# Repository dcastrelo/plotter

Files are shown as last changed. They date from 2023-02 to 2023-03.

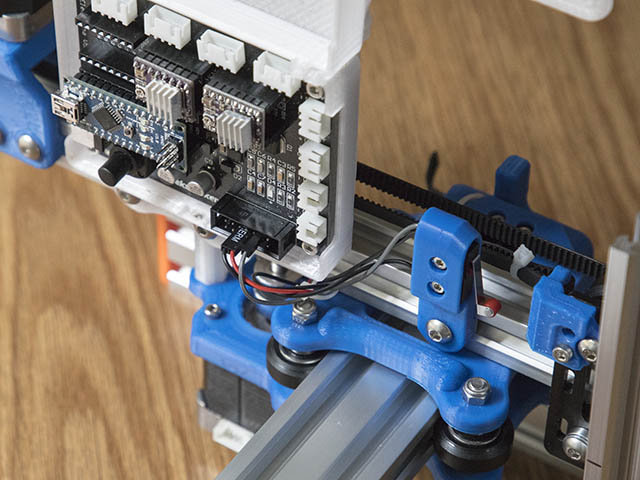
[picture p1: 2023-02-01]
images/IMG_1413_640x480.jpg

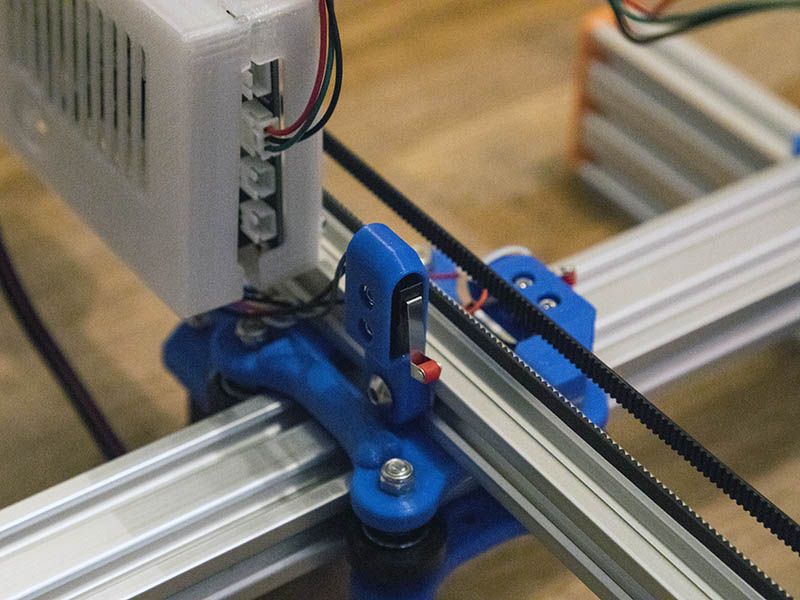
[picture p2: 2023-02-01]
images/IMG_1424_800x600.jpg

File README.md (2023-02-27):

# plotter para usar con laser o lo que sea

proyecto: https://openbuilds.com/builds/horizontal-cantilever-or-vertical-diode-laser-engraver.10031/
fork de https://www.thingiverse.com/thing:4934772

listado de partes: https://docs.google.com/spreadsheets/d/1wXE9ehnmEfAuOU7LIpCEzy9SvMc0fRSBS328PcNFEXU/edit?usp=sharing

Guia de armado
https://github.com/dcastrelo/plotter/blob/main/Assembly_Guide_for_Cantilever_Laser_Engraver_V821.2.pdf

vamos a hacer el modelo D_2040_2040

URL con info para lidiar con el firmware y poder usar el servo como Z

https://www.instructables.com/How-to-Control-a-Servo-Using-GRBL/

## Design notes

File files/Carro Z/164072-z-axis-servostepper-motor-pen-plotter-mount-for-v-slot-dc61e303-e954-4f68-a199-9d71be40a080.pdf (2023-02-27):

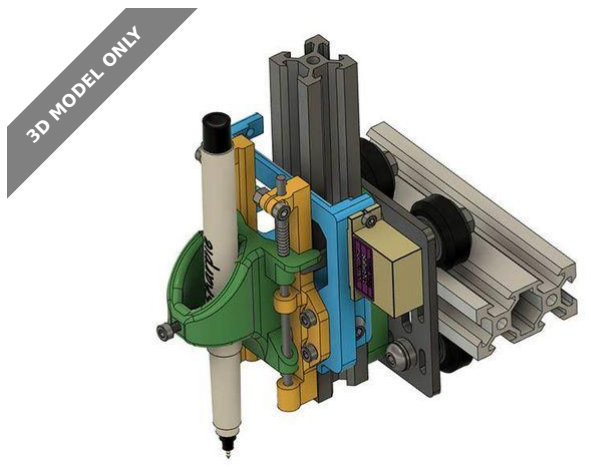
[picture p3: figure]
3D MODEL ONLY

# Summary

12/28/2020 Update: I added the file *RP_200411_Servo_Z_Dual_X.cfg**

that has my klipper configuration using the servo...

Art & Design (https://www.printables.com/model?categoryId=13) | > | Other Art & Designs (https://www.printables.com/model?categoryId=41)
Tags: fusion360 | arduino | penholder | penplotter | cncplotter

### 12/28/2020 Update:

I added the fileRP_200411_Servo_Z_Dual_X.cfg* that has my klipper

configuration using the servo for the Z-axis for reference.

Z-axis servo/Stepper motor Pen Plotter mount for V-Slot

I needed a pen mount for the Rolling Plotter I am designing and https://

www.thingiverse.com/thing:2349232 was pretty much what I wanted

except I needed it to mount to a 2020 V-slot. I redrew it in fusion 360 like it

was & then modified it to work for my design. I had some troubles getting

the servo to work with Marlin firmware, so I made a couple of other

mounts to use a nema17 pancake stepper & a 28BYJ-48 stepper motor. I

then found a way to use the servo with klipper firmware, but might use a

stepper motor later. I found the models of the servo, sharpie, & 28BYJ-48 geodave (https://www.printables.com/social/231754/about)

# Z-axis servo/ Stepper motor Pen Plotter mount for V-Slot

VIEW IN BROWSER (https://www.printables.com/model/164072-z-axis-servostepper-motor-pen-plotter-mount-for-v-)

updated 12. 4. 2022 | published 7. 4. 2022

stepper motor on grabcad, but didn't include them in the fusion 360

assembly file here.

The build log of my printer can be found here: https://openbuilds.com/

builds/a-rolling-plotter.9207/ (https://openbuilds.com/builds/a-rolling-plotter.9207/)

Here is a video of my plotter in action.

For any of the mounts print: Pen_V_Mount.stl

### V2020_Z_6_4mmShim_Plate.stl Base_Slide_Mount_Long.stl

orBase_Slide_Mount_Short.stl. The Long version is 5mm longer for

### looser spring V2020_Z_6_4mmShim_Plate.stl

4 -M3_Spacer.stl if using M3x16mm screws to mount Pen mount to V-slot

mount

For the servo mount style you can mount the servo on which ever side is

more convenient for you.

### Print: Z_Servo_SideMount_V2020.stl

### Edit theZ_Servo_SideMount_V2020.f3d file if you need to change any of

the design.

For the 28BYJ-48 motor mount you can also mount on which ever side is

more convenient for you.

### Print: Z_Mount_28BYJ-48_V2020.stl Horn_28BYJ-48.stl

### Edit theZ_28BYJ-48_SideMount_V2020.f3d file if you need to change

any of this design.

For the Nema17 pancake stepper mount, I only made a mount on one side,

but you can mirror the part if you want it on the other side.

### Print: Z_Nema17_Pancake_V2020.stl Horn_Nema17.stl

### Edit theZ_Nema17_Pancake_V2020.f3d file if you need to change any of

this design.

Depending on how deep your motor sits back, you might have to use the

4mm thicker*V2020_Z_10_4mmShim_Plate.stl rather than the 6.4mm plate

above. If you need more depth than that, you can edit
theV2020_Z_6_4mmShim_Plate v3.f3d to the size you need.

I printed all the files at .2mm layer height with eSun PLA+

I printed the Base_Slide_Mount with 4 perimeters & 30% infill

All the other parts I printed at 4 perimeters & 50% infill.

# Model files

I only used supports on the front ofPen_V_Mount.stl print.

I mounted the Base_slide to the V-slot mount with 4 - M3x16mm screws &

locknuts with a plastic 2mm washer.

2 - M3x10mm screws with locknuts to clamp down the M3 rods on the

slider

1 - M3x16mm screw & nut to clamp pen in place, you might want a longer

screw for smaller diameter pens.

2 or 4 - M5x12mm screws with T-nuts to mount to V-slot. Since pen is light,

I only used 2 screws

2 - M5x16mm screws with T-nuts to mount V2020_Z_6_4mmShim_Plate to

carriage.

I cut a 2020x250mm V-slot in half for the vertical V-Slot & using the

openbuilds V-Slot Gantry Plate-20mm for carriage which is 65mmx65mm.

The springs I took from pens from a dollar store. Those springs were rather

long, so I cut one in half & used half on each side. The M3 rods I took from

an old DVD drive as mentioned in the build I remixed this from.

I have only tested the servo mount, so let me know if you find a problem

with the other 2 mounts. I sized the nema17 pancake mount around the

pancake motor from zyltech.com. All pancake motors are not the same
depth.

Category: Art Tools

v2020_z_10_4mmshim_plate.stl

pen_v_mount.stl

z_nema17_pancake_v2020.f3d

base_slide_mount_long.stl

m3_spacer_v1.stl

z_servo_sidemount_v2020.stl

z_nema17_pancake_v2020.stl

z_28byj-48_sidemount_v2020.f3d

z_servo_sidemount_v2020.f3d

horn_28byj-48.stl

6mmplate_with_beltclamp_v31.stl

horn_nema17.stl

base_slide_mount_short.stl

Find source .stl files on Thingiverse.com (https://www.thingiverse.com/thing:4276609)

# License

This work is licensed under a

Creative Commons (4.0 International License)

Attribution (http://creativecommons.org/licenses/by/4.0/)

✖ | Sharing without ATTRIBUTION
✔ | Remix Culture allowed
✔ | Commercial Use
✔ | Free Cultural Works
✔ | Meets Open Definition

horn_28byj-48.f3d

v2020_z_6_4mmshim_plate.stl

v2020_z_6_4mmshim_plate_v3.f3d

z_mount_28byj-48_v2020.stl

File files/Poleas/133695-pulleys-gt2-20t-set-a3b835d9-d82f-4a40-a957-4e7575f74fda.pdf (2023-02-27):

## Pulleys GT2 - 20T

## set

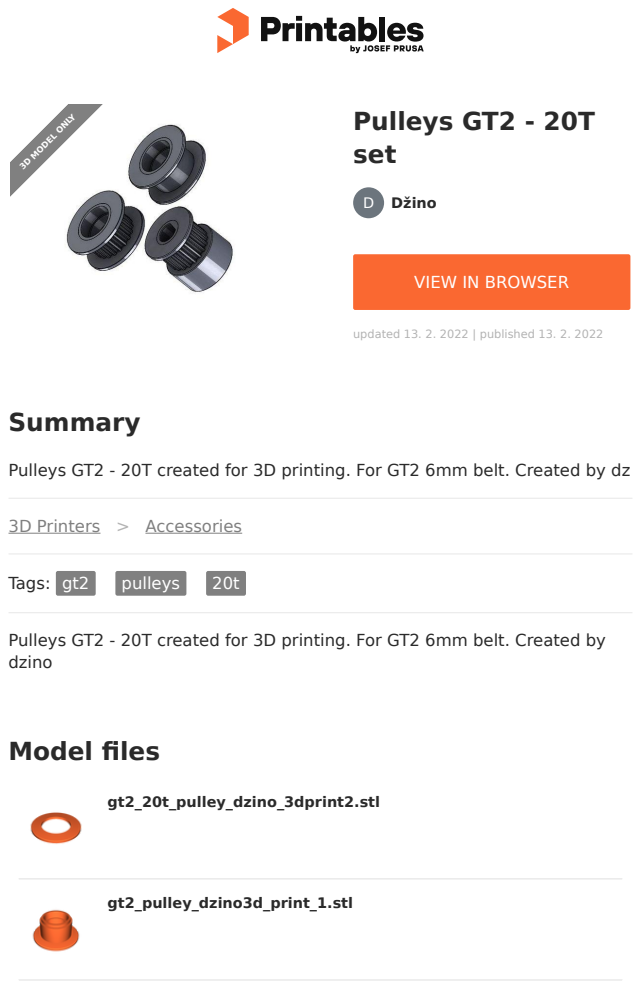
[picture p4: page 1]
Model files; Summary; 3D Printers; Accessories; Tags: gt2; pulleys; Džino; updated 13. 2. 2022 | published 13. 2. 2022; gt2_20t_pulley_dzino_3dprint2.stl; gt2_pulley_dzino3d_print_1.stl; 3D MODEL ONLY

VIEW IN BROWSER (https://www.printables.com/model/133695-pulleys-gt2-20t-set)

Pulleys GT2 - 20T created for 3D printing. For GT2 6mm belt. Created by dz

Pulleys GT2 - 20T created for 3D printing. For GT2 6mm belt. Created by
dzino

## License

This work is licensed under a
Creative Commons (4.0 International License)

Attribution—Noncommercial—Share Alike (http://creativecommons.org/licenses/by-nc-sa/4.0/) gt2_pulley_dzino3d_print_12.stl

gt2_pulley_dzino3d_print.stl

gt2_20t_pulley_dzino_3dprint12.stl

gt2_20t_dzino3d_print.stl

gt2_20t_pulley_dzino_3dprint.stl

gt2_20t_dzino3d_print_2.stl

gt2_pulley_dzino_3dprint2.stl

✖ | Sharing without ATTRIBUTION
✔ | Remix Culture allowed
✖ | Commercial Use
✖ | Free Cultural Works
✖ | Meets Open Definition

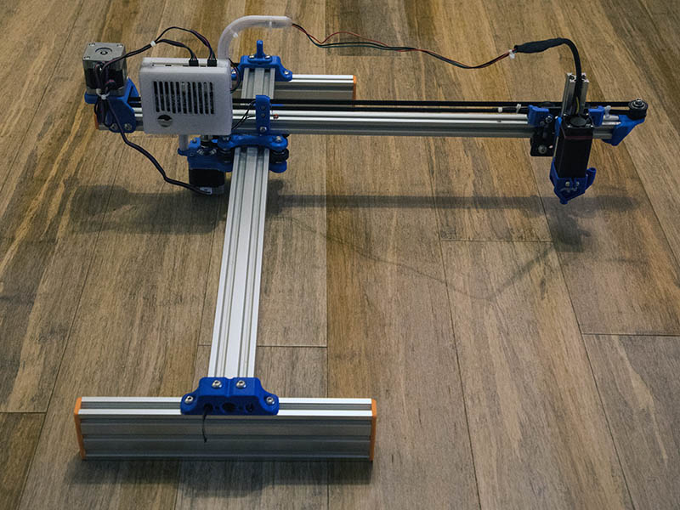
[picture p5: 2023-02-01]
images/IMG_1428_800x600.jpg

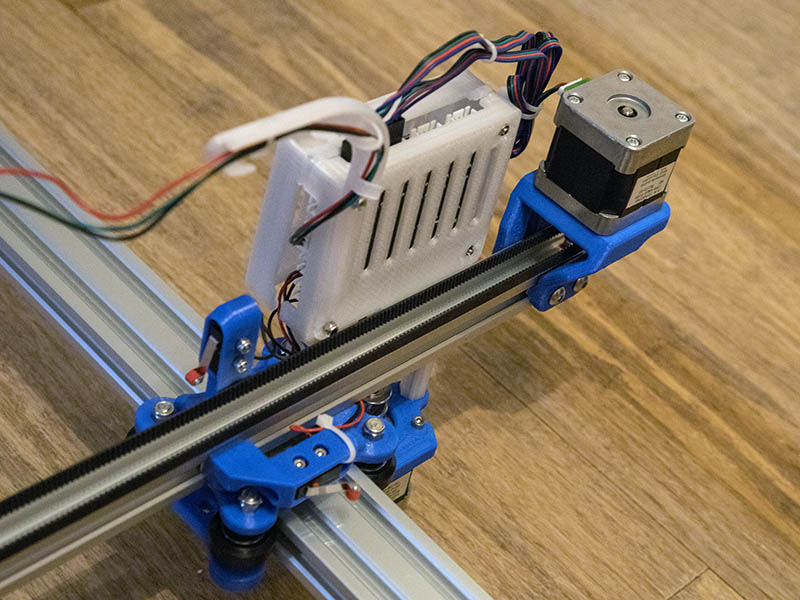
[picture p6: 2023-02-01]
images/IMG_1425_800x600.jpg

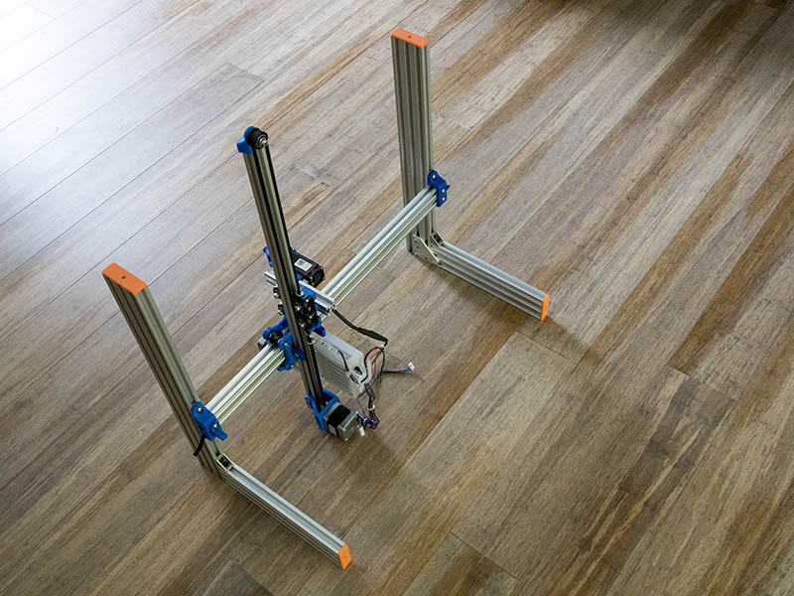
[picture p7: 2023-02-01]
images/IMG_1452_800x600.jpg

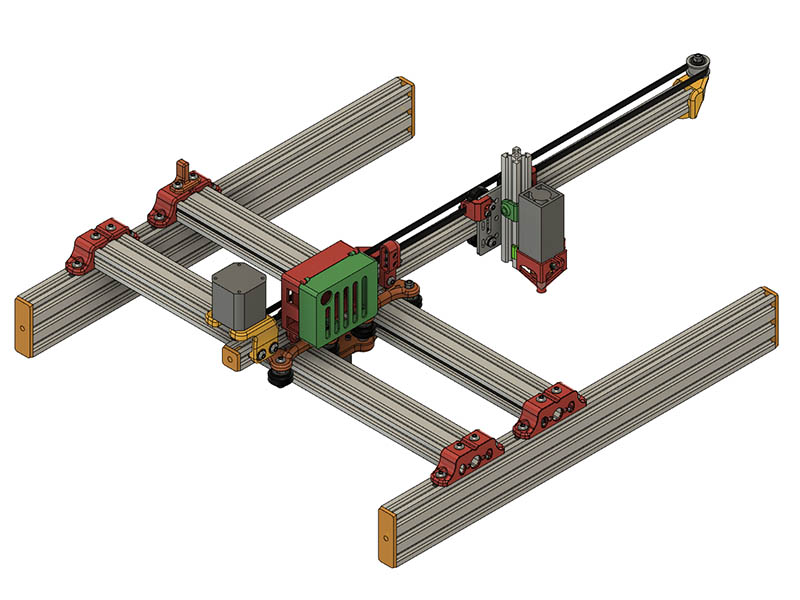
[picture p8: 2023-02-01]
images/D_2040x2040_Horizontal.jpg

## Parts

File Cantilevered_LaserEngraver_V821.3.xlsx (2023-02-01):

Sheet: A_2040_Horizontal
Cantilevered Laser Engraver BOM Version 821.1 (A_2040_Horizontal)
1 | V-Slot 2020x500mm | $5.49 |  | https://openbuildspartstore.com/v-slot-20x20-linear-rail/
1 | Zyltech Alternate 2020x600mm Source (This is what I used) | $5.45 | $5.45 | http://www.zyltech.com/zyltech-2020-v-groove-extrusion-pre-cut-lengths-300mm-2000mm/
1 | V-Slot 2020x250mm (cut in half for 125mm length Z-Axis) | $3.29 | $3.29 | https://openbuildspartstore.com/v-slot-20x20-linear-rail/
1 | V-Slot 2040x500mm | $6.99 |  | https://openbuildspartstore.com/v-slot-20x40-linear-rail/
1 | Zyltech Alternate 2040x600mm Source (This is what I used) | $5.95 | $5.95 | http://www.zyltech.com/zyltech-2040-v-groove-extrusion-pre-cut-lengths-300mm-2000mm/
2 | V-Slot 2060x250mm | $4.99 | $9.98 | https://openbuildspartstore.com/v-slot-20x60-linear-rail/
1 | V-Slot Gantry Plate - 20mm | $6.29 |  | https://openbuildspartstore.com/v-slot-gantry-plate-20mm/
1 | Zyltech Alternate Gantry Plate Silver for 20 Series V-Groove | $4.25 | $4.25 | Gantry Plate Silver for 20 Series V-Groove Extrusion - ZYLtech Engineering, LLC (https://www.zyltech.com/gantry-plate-silver-for-20-series-v-groove-extrusion/)
8 | Solid V-Wheel Kit | $5.19 |  | https://openbuildspartstore.com/solid-v-wheel-kit/
8 | Zyltech Alternate Wheel Source | $1.68 |  | http://www.zyltech.com/zyltech-20-series-wheel-pulley-bearing-for-2020-aluminum-extrusion-v-slot-compatible/
8 | AliExpress Alternate Source (Type B with Bearing) | $1.04 | $14.11 | https://www.aliexpress.com/item/32865660310.html
1 | Smooth Idler Pulley Kit | $5.99 | $5.99 | https://openbuildspartstore.com/smooth-idler-pulley-kit/
3 | M5 Tee Nuts (10 pack - 22 required) | $2.99 | $8.97 | https://openbuildspartstore.com/tee-nuts-m5-10-pack/
6 | Eccentric Spacers (2 on laser carriage & 4 on a front 2040 wheel) | $1.99 |  | https://openbuildspartstore.com/eccentric-spacer/
6 | Zyltech Alternate Eccentric Spacer source | $0.95 | $5.70 | http://www.zyltech.com/6mm-eccentric-nut-spacer-for-extrusion-carriage-wheels/
1 | Aluminum Spacers, 3mm (10 pack) only 2 spacers needed | $2.49 | $2.49 | https://openbuildspartstore.com/aluminum-spacers-10-pack/
1 | Aluminum Spacers, 6mm (10 pack) only 6 spacers needed | $3.39 | $3.39 | https://openbuildspartstore.com/aluminum-spacers-10-pack/
8 | Precision Shim - 10x5x1mm | $0.31 | $2.48 | https://openbuildspartstore.com/precision-shim-10x5x1mm/
19 | Socket Button Head M5x12mm Screws | $0.15 | $2.85 | https://www.boltdepot.com/Product-Details.aspx?product=6633
4 | Socket Button Head M5x16mm Screws (2 for X limit switch endstop & 2 for Z-axis shim plate) | $0.16 | $0.64 | https://www.boltdepot.com/Product-Details.aspx?product=6634
1 | Socket Button Head M5x25mm Screws (Idler pulley) | $0.21 | $0.21 | https://www.boltdepot.com/Product-Details.aspx?product=6636
4 | Socket Button Head M5x30mm Screws (Laser Carriage Wheels) | $0.25 | $1.00 | https://www.boltdepot.com/Product-Details.aspx?product=6637
5 | Socket Button Head M5x40mm Screws (Main Plate Wheels & 1 Tee Nut Mount) | $0.30 | $1.50 | https://www.boltdepot.com/Product-Details.aspx?product=6639
2 | Set Screw, Cup Point, M5x5mm (for 2040 Belt end T-nut clamp) | $0.08 | $0.16 | https://www.boltdepot.com/Product-Details.aspx?product=8721
9 | M5 Lock Nuts | $0.08 | $0.72 | https://www.boltdepot.com/Product-Details.aspx?product=4794
2 | M3 Locknuts | $0.06 | $0.12 | https://www.boltdepot.com/Product-Details.aspx?product=4792
12 | M3x10mm screws (Motor Mounts & laser mount) | $0.07 | $0.84 | https://www.boltdepot.com/Product-Details.aspx?product=6380
2 | M3x12mm screws (for carriage belt clamps) | $0.07 | $0.14 | https://www.boltdepot.com/Product-Details.aspx?product=6381
4 | M2.5x12mm screws (optional mechanical limit switches)
4 | M2.5 locknuts (optional mechanical limit switches)
1 | GT2 Timing Pulley 20Teeth (5 Pcs) only 2 required | $8.98 | $8.98 | https://www.amazon.com/gp/product/B077GNZK3J
1 | keystudio cnc shield v4 | $3.14 | $3.14 | https://www.aliexpress.com/item/32783418818.html
1 | EleksMaker Mana 3 Axis Stepper Motor Driver Controller Board (Alternate Choice) | $31.01 |  | https://www.aliexpress.com/item/33025259446.html
1 | Arduino Nano | $4.82 | $4.82 | https://www.aliexpress.com/item/32848298184.html
1 | Compatible UNO R3 Arduino Alternate | $5.95 |  | https://www.zyltech.com/zyltech-uno-r3-atmega328p-atmega16u2-for-arduino-w-free-usb-cable/
1 | CNC Shield for Arduino Alternate | $4.95 |  | https://www.zyltech.com/cnc-shield-for-arduino/
2 | DRV8825 stepper Drivers | $0.93 | $2.45 | https://www.aliexpress.com/item/4000386097983.html
1 | 12v power supply (5amp should be sufficient) | $7.98 | $7.98 | https://www.aliexpress.com/item/33014935336.html
2 | Nema 17 Motors | $8.99 | $17.98 | https://www.amazon.com/Twotrees-Stepper-17HS4401-Connector-Printer/dp/B07THK76QQ?th=1
1 | 6000mW 450nm Blue Light laser Head | $46.72 | $46.72 | https://www.aliexpress.com/item/4000214959199.html
1 | 5m of GT2x6mm | $3.04 | $3.04 | https://www.aliexpress.com/item/32619587350.html
4 | Wire ties for belt on cantilever belt
 |  |  | $175.34

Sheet: B_2040x2020_Horizontal
Cantilevered Laser Engraver BOM Version 821.1 (B_2040x2020_Horizontal)
1 | V-Slot 2020x500mm | $5.49 |  | https://openbuildspartstore.com/v-slot-20x20-linear-rail/
2 | Zyltech Alternate 2020x600mm Source (This is what I used) | $5.45 | $10.90 | http://www.zyltech.com/zyltech-2020-v-groove-extrusion-pre-cut-lengths-300mm-2000mm/
1 | V-Slot 2020x250mm (cut in half for 125mm length Z-Axis) | $3.29 | $3.29 | https://openbuildspartstore.com/v-slot-20x20-linear-rail/
1 | V-Slot 2040x500mm | $6.99 |  | https://openbuildspartstore.com/v-slot-20x40-linear-rail/
1 | Zyltech Alternate 2040x600mm Source (This is what I used) | $5.95 | $5.95 | http://www.zyltech.com/zyltech-2040-v-groove-extrusion-pre-cut-lengths-300mm-2000mm/
2 | V-Slot 2060x250mm (You can go with either 250mm or 500mm length, drawing shows 500mm) | $4.99 | $9.98 | https://openbuildspartstore.com/v-slot-20x60-linear-rail/
1 | V-Slot Gantry Plate - 20mm | $6.29 |  | https://openbuildspartstore.com/v-slot-gantry-plate-20mm/
1 | Zyltech Alternate Gantry Plate Silver for 20 Series V-Groove | $4.25 | $4.25 | Gantry Plate Silver for 20 Series V-Groove Extrusion - ZYLtech Engineering, LLC (https://www.zyltech.com/gantry-plate-silver-for-20-series-v-groove-extrusion/)
12 | Solid V-Wheel Kit | $5.19 |  | https://openbuildspartstore.com/solid-v-wheel-kit/
12 | Zyltech Alternate Wheel Source | $1.68 |  | http://www.zyltech.com/zyltech-20-series-wheel-pulley-bearing-for-2020-aluminum-extrusion-v-slot-compatible/
12 | AliExpress Alternate Source (Type B with Bearing) | $1.04 | $18.27 | https://www.aliexpress.com/item/32865660310.html
1 | Smooth Idler Pulley Kit | $5.99 | $5.99 | https://openbuildspartstore.com/smooth-idler-pulley-kit/
3 | M5 Tee Nuts (10 pack - 29 required) | $2.99 | $8.97 | https://openbuildspartstore.com/tee-nuts-m5-10-pack/
8 | Eccentric Spacers (2 on laser carriage & 4 on a front 2040 wheel) | $1.99 |  | https://openbuildspartstore.com/eccentric-spacer/
8 | Zyltech Alternate Eccentric Spacer source | $0.95 | $7.60 | http://www.zyltech.com/6mm-eccentric-nut-spacer-for-extrusion-carriage-wheels/
1 | Aluminum Spacers, 3mm (10 pack) only 2 spacers needed | $2.49 | $2.49 | https://openbuildspartstore.com/aluminum-spacers-10-pack/
1 | Aluminum Spacers, 6mm (10 pack) only 8 spacers needed | $3.39 | $3.39 | https://openbuildspartstore.com/aluminum-spacers-10-pack/
8 | Precision Shim - 10x5x1mm | $0.31 | $2.48 | https://openbuildspartstore.com/precision-shim-10x5x1mm/
26 | Socket Button Head M5x12mm Screws | $0.15 | $3.90 | https://www.boltdepot.com/Product-Details.aspx?product=6633
4 | Socket Button Head M5x16mm Screws (2 for X limit switch endstop & 2 for Z-axis shim plate) | $0.16 | $0.64 | https://www.boltdepot.com/Product-Details.aspx?product=6634
1 | Socket Button Head M5x25mm Screws (Idler pulley) | $0.21 | $0.21 | https://www.boltdepot.com/Product-Details.aspx?product=6636
8 | Socket Button Head M5x30mm Screws (Laser Carriage Wheels) | $0.25 | $2.00 | https://www.boltdepot.com/Product-Details.aspx?product=6637
5 | Socket Button Head M5x40mm Screws (Main Plate Wheels & 1 Tee Nut Mount) | $0.30 | $1.50 | https://www.boltdepot.com/Product-Details.aspx?product=6639
2 | Set Screw, Cup Point, M5x5mm (for 2040 Belt end T-nut clamp) | $0.08 | $0.16 | https://www.boltdepot.com/Product-Details.aspx?product=8721
13 | M5 Lock Nuts | $0.08 | $1.04 | https://www.boltdepot.com/Product-Details.aspx?product=4794
2 | M3 Locknuts | $0.06 | $0.12 | https://www.boltdepot.com/Product-Details.aspx?product=4792
12 | M3x10mm screws (Motor Mounts & laser mount) | $0.07 | $0.84 | https://www.boltdepot.com/Product-Details.aspx?product=6380
2 | M3x12mm screws (for carriage belt clamps) | $0.07 | $0.14 | https://www.boltdepot.com/Product-Details.aspx?product=6381
4 | M2.5x12mm screws (optional mechanical limit switches)
4 | M2.5 locknuts (optional mechanical limit switches)
1 | GT2 Timing Pulley 20Teeth (5 Pcs) only 2 required | $8.98 | $8.98 | https://www.amazon.com/gp/product/B077GNZK3J
1 | keystudio cnc shield v4 | $3.14 | $3.14 | https://www.aliexpress.com/item/32783418818.html
1 | EleksMaker Mana 3 Axis Stepper Motor Driver Controller Board (Alternate Choice) | $31.01 |  | https://www.aliexpress.com/item/33025259446.html
1 | Arduino Nano | $4.82 | $4.82 | https://www.aliexpress.com/item/32848298184.html
1 | Compatible UNO R3 Arduino Alternate | $5.95 |  | https://www.zyltech.com/zyltech-uno-r3-atmega328p-atmega16u2-for-arduino-w-free-usb-cable/
1 | CNC Shield for Arduino Alternate | $4.95 |  | https://www.zyltech.com/cnc-shield-for-arduino/
2 | DRV8825 stepper Drivers | $0.93 | $2.45 | https://www.aliexpress.com/item/4000386097983.html
1 | 12v power supply (5amp should be sufficient) | $7.98 | $7.98 | https://www.aliexpress.com/item/33014935336.html
2 | Nema 17 Motors | $8.99 | $17.98 | https://www.amazon.com/Twotrees-Stepper-17HS4401-Connector-Printer/dp/B07THK76QQ?th=1
1 | 6000mW 450nm Blue Light laser Head | $46.72 | $46.72 | https://www.aliexpress.com/item/4000214959199.html
1 | 5m of GT2x6mm | $3.04 | $3.04 | https://www.aliexpress.com/item/32619587350.html
4 | Wire ties for belt on cantilever belt
 |  |  | $189.22

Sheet: C_2020x2020_Horizontal
Cantilevered Laser Engraver BOM Version 821.1 (C_2020x2020_Horizontal)
1 | V-Slot 2020x500mm | $5.49 |  | https://openbuildspartstore.com/v-slot-20x20-linear-rail/
3 | Zyltech Alternate 2020x600mm Source (This is what I used) | $5.45 | $16.35 | http://www.zyltech.com/zyltech-2020-v-groove-extrusion-pre-cut-lengths-300mm-2000mm/
1 | V-Slot 2020x250mm (cut in half for 125mm length Z-Axis) | $3.29 | $3.29 | https://openbuildspartstore.com/v-slot-20x20-linear-rail/
2 | V-Slot 2060x250mm (You can go with either 250mm or 500mm length, drawing shows 500mm) | $4.99 | $9.98 | https://openbuildspartstore.com/v-slot-20x60-linear-rail/
1 | V-Slot Gantry Plate - 20mm | $6.29 |  | https://openbuildspartstore.com/v-slot-gantry-plate-20mm/
1 | Zyltech Alternate Gantry Plate Silver for 20 Series V-Groove | $4.25 | $4.25 | Gantry Plate Silver for 20 Series V-Groove Extrusion - ZYLtech Engineering, LLC (https://www.zyltech.com/gantry-plate-silver-for-20-series-v-groove-extrusion/)
12 | Solid V-Wheel Kit | $5.19 |  | https://openbuildspartstore.com/solid-v-wheel-kit/
12 | Zyltech Alternate Wheel Source | $1.68 |  | http://www.zyltech.com/zyltech-20-series-wheel-pulley-bearing-for-2020-aluminum-extrusion-v-slot-compatible/
12 | AliExpress Alternate Source (Type B with Bearing) | $1.04 | $18.27 | https://www.aliexpress.com/item/32865660310.html
1 | Smooth Idler Pulley Kit | $5.99 | $5.99 | https://openbuildspartstore.com/smooth-idler-pulley-kit/
3 | M5 Tee Nuts (10 pack - 27 required) | $2.99 | $8.97 | https://openbuildspartstore.com/tee-nuts-m5-10-pack/
8 | Eccentric Spacers (2 on laser carriage & 4 on a front 2040 wheel) | $1.99 |  | https://openbuildspartstore.com/eccentric-spacer/
8 | Zyltech Alternate Eccentric Spacer source | $0.95 | $7.60 | http://www.zyltech.com/6mm-eccentric-nut-spacer-for-extrusion-carriage-wheels/
1 | Aluminum Spacers, 3mm (10 pack) only 2 spacers needed | $2.49 | $2.49 | https://openbuildspartstore.com/aluminum-spacers-10-pack/
1 | Aluminum Spacers, 6mm (10 pack) only 8 spacers needed | $3.39 | $3.39 | https://openbuildspartstore.com/aluminum-spacers-10-pack/
8 | Precision Shim - 10x5x1mm | $0.31 | $2.48 | https://openbuildspartstore.com/precision-shim-10x5x1mm/
25 | Socket Button Head M5x12mm Screws | $0.15 | $3.75 | https://www.boltdepot.com/Product-Details.aspx?product=6633
4 | Socket Button Head M5x16mm Screws (2 for X limit switch endstop & 2 for Z-axis shim plate) | $0.16 | $0.64 | https://www.boltdepot.com/Product-Details.aspx?product=6634
1 | Socket Button Head M5x25mm Screws (Idler pulley) | $0.21 | $0.21 | https://www.boltdepot.com/Product-Details.aspx?product=6636
8 | Socket Button Head M5x30mm Screws (Laser Carriage Wheels) | $0.25 | $2.00 | https://www.boltdepot.com/Product-Details.aspx?product=6637
5 | Socket Button Head M5x40mm Screws (Main Plate Wheels & 1 Tee Nut Mount) | $0.30 | $1.50 | https://www.boltdepot.com/Product-Details.aspx?product=6639
2 | Set Screw, Cup Point, M5x5mm (for 2040 Belt end T-nut clamp) | $0.08 | $0.16 | https://www.boltdepot.com/Product-Details.aspx?product=8721
13 | M5 Lock Nuts | $0.08 | $1.04 | https://www.boltdepot.com/Product-Details.aspx?product=4794
2 | M3 Locknuts | $0.06 | $0.12 | https://www.boltdepot.com/Product-Details.aspx?product=4792
12 | M3x10mm screws (Motor Mounts & laser mount) | $0.07 | $0.84 | https://www.boltdepot.com/Product-Details.aspx?product=6380
2 | M3x12mm screws (for carriage belt clamps) | $0.07 | $0.14 | https://www.boltdepot.com/Product-Details.aspx?product=6381
4 | M2.5x12mm screws (optional mechanical limit switches)
4 | M2.5 locknuts (optional mechanical limit switches)
1 | GT2 Timing Pulley 20Teeth (5 Pcs) only 2 required | $8.98 | $8.98 | https://www.amazon.com/gp/product/B077GNZK3J
1 | keystudio cnc shield v4 | $3.14 | $3.14 | https://www.aliexpress.com/item/32783418818.html
1 | EleksMaker Mana 3 Axis Stepper Motor Driver Controller Board (Alternate Choice) | $31.01 |  | https://www.aliexpress.com/item/33025259446.html
1 | Arduino Nano | $4.82 | $4.82 | https://www.aliexpress.com/item/32848298184.html
1 | Compatible UNO R3 Arduino Alternate | $5.95 |  | https://www.zyltech.com/zyltech-uno-r3-atmega328p-atmega16u2-for-arduino-w-free-usb-cable/
1 | CNC Shield for Arduino Alternate | $4.95 |  | https://www.zyltech.com/cnc-shield-for-arduino/
2 | DRV8825 stepper Drivers | $0.93 | $2.45 | https://www.aliexpress.com/item/4000386097983.html
1 | 12v power supply (5amp should be sufficient) | $7.98 | $7.98 | https://www.aliexpress.com/item/33014935336.html
2 | Nema 17 Motors | $8.99 | $17.98 | https://www.amazon.com/Twotrees-Stepper-17HS4401-Connector-Printer/dp/B07THK76QQ?th=1
1 | 6000mW 450nm Blue Light laser Head | $46.72 | $46.72 | https://www.aliexpress.com/item/4000214959199.html
1 | 5m of GT2x6mm | $3.04 | $3.04 | https://www.aliexpress.com/item/32619587350.html
4 | Wire ties for belt on cantilever belt
 |  |  | $188.57

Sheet: D_2040x2040_Horizontal
Cantilevered Laser Engraver BOM Version 821.3 (D_2040x2040_Horizontal)
1 | V-Slot 2020x500mm | $5.49 | $5.49 | https://openbuildspartstore.com/v-slot-20x20-linear-rail/?ref=PiXgOsvJGqfl
1 | Zyltech Alternate 2020x600mm Source | $5.45 |  | http://www.zyltech.com/zyltech-2020-v-groove-extrusion-pre-cut-lengths-300mm-2000mm/
1 | V-Slot 2020x250mm (cut in half for 125mm length Z-Axis) | $3.29 | $3.29 | https://openbuildspartstore.com/v-slot-20x20-linear-rail/?ref=PiXgOsvJGqfl
2 | V-Slot 2040x500mm | $6.99 | $13.98 | https://openbuildspartstore.com/v-slot-20x40-linear-rail/?ref=PiXgOsvJGqfl
1 | Zyltech Alternate 2040x600mm Source | $5.95 |  | http://www.zyltech.com/zyltech-2040-v-groove-extrusion-pre-cut-lengths-300mm-2000mm/
2 | V-Slot 2060x250mm (You can go with either 250mm or 500mm length, drawing shows 500mm) | $4.99 | $9.98 | https://openbuildspartstore.com/v-slot-20x60-linear-rail/?ref=PiXgOsvJGqfl
1 | V-Slot Gantry Plate - 20mm | $6.29 | $6.29 | https://openbuildspartstore.com/v-slot-gantry-plate-20mm/?ref=PiXgOsvJGqfl
1 | Zyltech Alternate Gantry Plate Silver for 20 Series V-Groove | $4.25 |  | Gantry Plate Silver for 20 Series V-Groove Extrusion - ZYLtech Engineering, LLC (https://www.zyltech.com/gantry-plate-silver-for-20-series-v-groove-extrusion/)
12 | Solid V-Wheel Kit | $5.19 | $62.28 | https://openbuildspartstore.com/solid-v-wheel-kit/?ref=PiXgOsvJGqfl
8 | Zyltech Alternate Wheel Source | $1.68 |  | http://www.zyltech.com/zyltech-20-series-wheel-pulley-bearing-for-2020-aluminum-extrusion-v-slot-compatible/
8 | AliExpress Alternate Source (Type B with Bearing) | $1.04 |  | https://www.aliexpress.com/item/32865660310.html
1 | Smooth Idler Pulley Kit | $5.99 | $5.99 | https://openbuildspartstore.com/smooth-idler-pulley-kit/?ref=PiXgOsvJGqfl
4 | M5 Tee Nuts (10 pack - 31 required) | $2.99 | $11.96 | https://openbuildspartstore.com/tee-nuts-m5-10-pack/?ref=PiXgOsvJGqfl
8 | Eccentric Spacers (2 on laser carriage & 4 on a front 2040 wheel) | $1.99 | $15.92 | https://openbuildspartstore.com/eccentric-spacer/?ref=PiXgOsvJGqfl
8 | Zyltech Alternate Eccentric Spacer source | $0.95 |  | http://www.zyltech.com/6mm-eccentric-nut-spacer-for-extrusion-carriage-wheels/
1 | Aluminum Spacers, 3mm (10 pack) only 2 spacers needed | $2.49 | $2.49 | https://openbuildspartstore.com/aluminum-spacers-10-pack/?ref=PiXgOsvJGqfl
1 | Aluminum Spacers, 6mm (10 pack) only 8 spacers needed | $3.39 | $3.39 | https://openbuildspartstore.com/aluminum-spacers-10-pack/?ref=PiXgOsvJGqfl
8 | Precision Shim - 10x5x1mm | $0.31 | $2.48 | https://openbuildspartstore.com/precision-shim-10x5x1mm/?ref=PiXgOsvJGqfl
 |  |  | $143.54
28 | Socket Button Head M5x12mm Screws | $0.17 | $4.76 | https://www.boltdepot.com/Product-Details.aspx?product=6633
4 | Socket Button Head M5x16mm Screws (2 for X limit switch endstop & 2 for Z-axis shim plate) | $0.19 | $0.76 | https://www.boltdepot.com/Product-Details.aspx?product=6634
1 | Socket Button Head M5x25mm Screws (Idler pulley) | $0.24 | $0.24 | https://www.boltdepot.com/Product-Details.aspx?product=6636
8 | Socket Button Head M5x30mm Screws (Laser Carriage Wheels) | $0.29 | $2.32 | https://www.boltdepot.com/Product-Details.aspx?product=6637
5 | Socket Button Head M5x40mm Screws (Main Plate Wheels & 1 Tee Nut Mount) | $0.34 | $1.70 | https://www.boltdepot.com/Product-Details.aspx?product=6639
2 | Set Screw, Cup Point, M5x5mm (for 2040 Belt end T-nut clamp) | $0.09 | $0.18 | https://www.boltdepot.com/Product-Details.aspx?product=8721
13 | M5 Lock Nuts | $0.09 | $1.17 | https://www.boltdepot.com/Product-Details.aspx?product=4794
2 | M3 Locknuts | $0.07 | $0.14 | https://www.boltdepot.com/Product-Details.aspx?product=4792
12 | M3x10mm screws (Motor Mounts & laser mount) | $0.08 | $0.96 | https://www.boltdepot.com/Product-Details.aspx?product=6380
2 | M3x12mm screws (for carriage belt clamps) | $0.08 | $0.16 | https://www.boltdepot.com/Product-Details.aspx?product=6381
1 | M2.5x12mm screws (50 pack) (optional mechanical limit switches) | $1.40 |  | https://www.aliexpress.com/item/1005001975621423.html
1 | M2.5 locknuts (50 pack) (optional mechanical limit switches) | $2.71 |  | https://www.aliexpress.com/item/32985781753.html
 |  |  | $12.39
1 | GT2 Timing Pulley 20Teeth (5 Pcs) only 2 required | $8.98 | $8.98 | https://www.amazon.com/gp/product/B077GNZK3J
1 | EleksMaker Mana 3 Axis Stepper Motor Driver Controller Board (What I am using) | $35.92 |  | https://www.aliexpress.com/item/33025259446.html
1 | Compatible UNO R3 Arduino Alternate | $5.95 | $5.95 | https://www.zyltech.com/zyltech-uno-r3-atmega328p-atmega16u2-for-arduino-w-free-usb-cable/
1 | CNC Shield for Arduino Alternate | $3.95 | $3.95 | https://www.zyltech.com/cnc-shield-for-arduino/
1 | DRV8825 stepper Drivers (3 Pack, only 2 needed) | $7.95 | $7.95 | https://www.zyltech.com/drv8825-stepper-motor-driver-module-3-4-or-5-pack/
1 | 12v power supply (5amp should be sufficient) | $7.98 | $7.98 | https://www.aliexpress.com/item/33014935336.html
2 | Nema 17 Motors | $8.99 | $17.98 | https://www.amazon.com/Twotrees-Stepper-17HS4401-Connector-Printer/dp/B07THK76QQ?th=1
1 | 6000mW 450nm Blue Light laser Head | $46.72 | $46.72 | https://www.aliexpress.com/item/4000214959199.html
1 | 5m of GT2x6mm | $3.04 | $3.04 | https://www.aliexpress.com/item/32619587350.html
4 | Wire ties for belt on cantilever belt
 |  |  | $102.55
 | Total |  | $258.48

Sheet: E_2040_HorizontalVertical
Cantilevered Laser Engraver BOM Version 821.1
2 | V-Slot 2020x500mm | $5.49 |  | https://openbuildspartstore.com/v-slot-20x20-linear-rail/
2 | Zyltech Alternate 2020x600mm Source (This is what I used) | $5.45 | $10.90 | http://www.zyltech.com/zyltech-2020-v-groove-extrusion-pre-cut-lengths-300mm-2000mm/
1 | V-Slot 2020x250mm (cut in half for 125mm length Z-Axis) | $3.29 | $3.29 | https://openbuildspartstore.com/v-slot-20x20-linear-rail/
1 | V-Slot 2040x500mm | $6.99 |  | https://openbuildspartstore.com/v-slot-20x40-linear-rail/
1 | Zyltech Alternate 2040x600mm Source (This is what I used) | $5.95 | $5.95 | http://www.zyltech.com/zyltech-2040-v-groove-extrusion-pre-cut-lengths-300mm-2000mm/
2 | V-Slot 2060x500mm | $9.99 | $19.98 | https://openbuildspartstore.com/v-slot-20x60-linear-rail/
2 | V-Slot 2060x250mm | $4.99 | $9.98 | https://openbuildspartstore.com/v-slot-20x60-linear-rail/
1 | V-Slot Gantry Plate - 20mm | $6.29 |  | https://openbuildspartstore.com/v-slot-gantry-plate-20mm/
1 | Zyltech Alternate Gantry Plate Silver for 20 Series V-Groove | $4.25 | $4.25 | Gantry Plate Silver for 20 Series V-Groove Extrusion - ZYLtech Engineering, LLC (https://www.zyltech.com/gantry-plate-silver-for-20-series-v-groove-extrusion/)
2 | Cast Corner Bracket | $1.49 | $2.98 | https://openbuildspartstore.com/cast-corner-bracket/
2 | 2020 Extrusion 90° Plate Bracket (Connect 2060x250Vertical foot to 2060x500mm foot) | $1.95 | $3.90 | https://www.zyltech.com/2020-extrusion-90-plate-bracket/
8 | Solid V-Wheel Kit | $5.19 |  | https://openbuildspartstore.com/solid-v-wheel-kit/
8 | Zyltech Alternate Wheel Source | $1.68 |  | http://www.zyltech.com/zyltech-20-series-wheel-pulley-bearing-for-2020-aluminum-extrusion-v-slot-compatible/
8 | AliExpress Alternate Source (Type B with Bearing) | $1.04 | $14.11 | https://www.aliexpress.com/item/32865660310.html
1 | Smooth Idler Pulley Kit | $5.99 | $5.99 | https://openbuildspartstore.com/smooth-idler-pulley-kit/
4 | M5 Tee Nuts (10 pack - 36 required) | $2.99 | $11.96 | https://openbuildspartstore.com/tee-nuts-m5-10-pack/
6 | Eccentric Spacers (2 on laser carriage & 4 on a front 2040 wheel) | $1.99 |  | https://openbuildspartstore.com/eccentric-spacer/
6 | Zyltech Alternate Eccentric Spacer source | $0.95 | $5.70 | http://www.zyltech.com/6mm-eccentric-nut-spacer-for-extrusion-carriage-wheels/
1 | Aluminum Spacers, 3mm (10 pack) only 2 spacers needed | $2.49 | $2.49 | https://openbuildspartstore.com/aluminum-spacers-10-pack/
1 | Aluminum Spacers, 6mm (10 pack) only 6 spacers needed | $3.39 | $3.39 | Aluminum Spacers (10 Pack) - OpenBuilds Part Store (https://openbuildspartstore.com/aluminum-spacers-10-pack/)
8 | Precision Shim - 10x5x1mm | $0.31 | $2.48 | https://openbuildspartstore.com/precision-shim-10x5x1mm/
10 | Socket Button Head M5x8mm Screws | $0.13 | $1.30 | https://www.boltdepot.com/Product-Details.aspx?product=6631
18 | Socket Button Head M5x12mm Screws | $0.13 | $2.34 | https://www.boltdepot.com/Product-Details.aspx?product=6633
4 | Socket Button Head M5x16mm Screws (2 for X limit switch endstop & 2 for Z-axis shim plate) | $0.16 | $0.64 | https://www.boltdepot.com/Product-Details.aspx?product=6634
1 | Socket Button Head M5x25mm Screws | $0.18 | $0.18 | https://www.boltdepot.com/Product-Details.aspx?product=6636
4 | Socket Button Head M5x30mm Screws | $0.22 | $0.88 | https://www.boltdepot.com/Product-Details.aspx?product=6637
5 | Socket Button Head M5x40mm Screws | $0.26 | $1.30 | https://www.boltdepot.com/Product-Details.aspx?product=6639
2 | Set Screw, Cup Point, M5x5mm (for 2040 Belt end T-nut clamp) | $0.08 | $0.16 | https://www.boltdepot.com/Product-Details.aspx?product=8721
9 | M5 Lock Nuts | $0.07 | $0.63 | https://www.boltdepot.com/Product-Details.aspx?product=4794
2 | M3 Locknuts | $0.05 | $0.10 | https://www.boltdepot.com/Product-Details.aspx?product=4792
12 | M3x10mm screws (Motor Mounts & laser mount) | $0.06 | $0.72 | https://www.boltdepot.com/Product-Details.aspx?product=6380
2 | M3x12mm screws (for carriage belt clamps) | $0.07 | $0.14 | https://www.boltdepot.com/Product-Details.aspx?product=6381
4 | M2.5x12mm screws (optional mechanical limit switches)
4 | M2.5 locknuts (optional mechanical limit switches)
1 | GT2 Timing Pulley 20Teeth (5 Pcs) only 2 required | $8.98 | $8.98 | https://www.amazon.com/gp/product/B077GNZK3J
1 | keystudio cnc shield v4 | $3.14 | $3.14 | https://www.aliexpress.com/item/32783418818.html
 | EleksMaker Mana 3 Axis Stepper Motor Driver Controller Board (Alternate Choice) | $31.01 |  | https://www.aliexpress.com/item/33025259446.html
1 | Arduino Nano | $4.78 | $4.78 | https://www.aliexpress.com/item/32848298184.html
 | Compatible UNO R3 Arduino Alternate | $5.95 |  | https://www.zyltech.com/zyltech-uno-r3-atmega328p-atmega16u2-for-arduino-w-free-usb-cable/
 | CNC Shield for Arduino Alternate | $4.95 |  | https://www.zyltech.com/cnc-shield-for-arduino/
2 | DRV8825 stepper Drivers | $0.93 | $2.45 | https://www.aliexpress.com/item/4000386097983.html
1 | 12v power supply (5amp should be sufficient) | $7.98 | $7.98 | https://www.aliexpress.com/item/33014935336.html
2 | Nema 17 Motors | $8.99 | $17.98 | https://www.amazon.com/Twotrees-Stepper-17HS4401-Connector-Printer/dp/B07THK76QQ?th=1
1 | 6000mW 450nm Blue Light laser Head | $45.99 | $45.99 | https://www.aliexpress.com/item/4000214959199.html
1 | 5m of GT2x6mm | $3.04 | $3.04 | https://www.aliexpress.com/item/32619587350.html
4 | Wire ties for belt on cantilever belt
 |  |  | $210.08

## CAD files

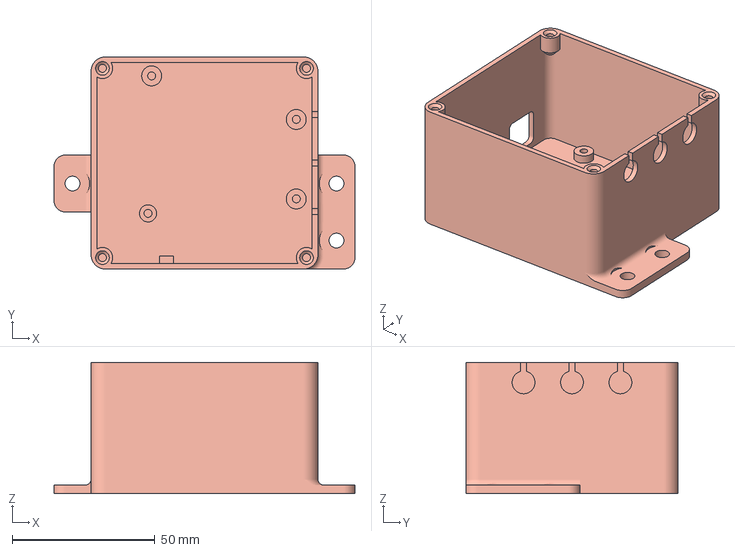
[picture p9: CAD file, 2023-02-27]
files/Arduino CNC Case/DC/Case Box.3mf
105.6 x 74.4 x 46.0 mm

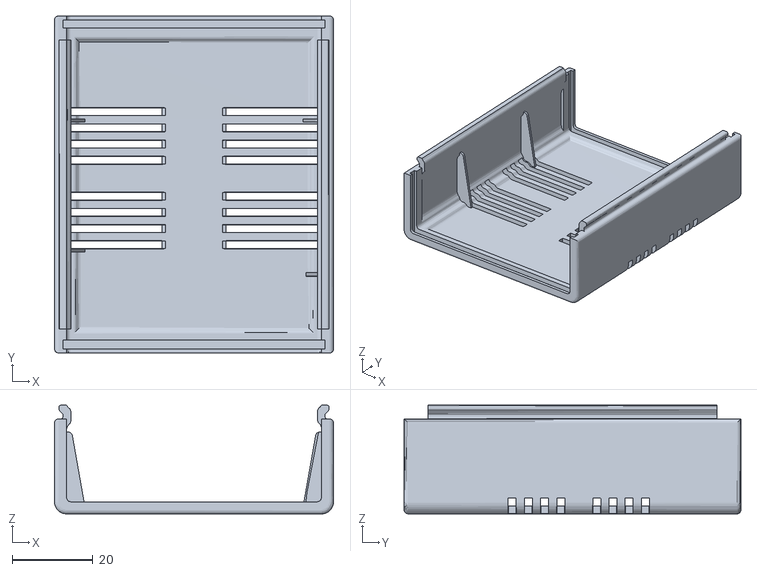
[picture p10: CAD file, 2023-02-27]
files/Arduino CNC Case/UnoCNC_CaseTop.stl
69.0 x 83.3 x 26.9

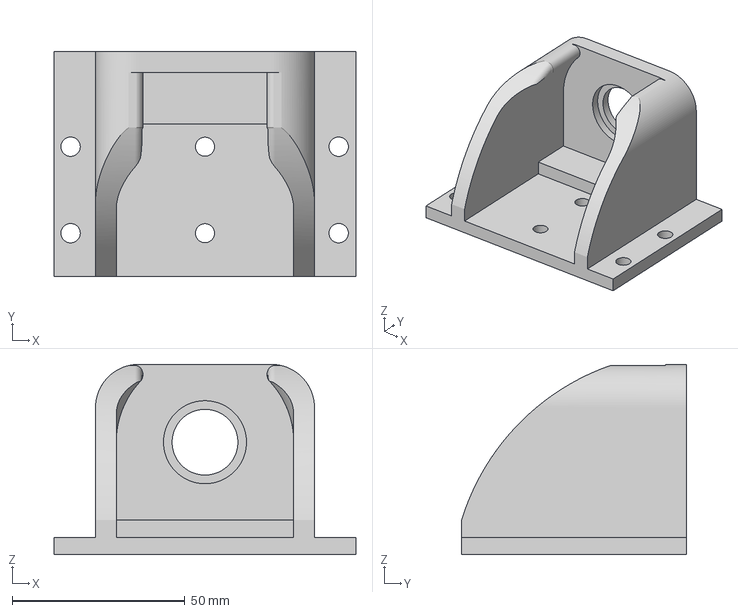
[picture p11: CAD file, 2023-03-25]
files/Carro Z/carro Z DC/soporte dremel versa.3mf
87.3 x 65.0 x 55.0 mm

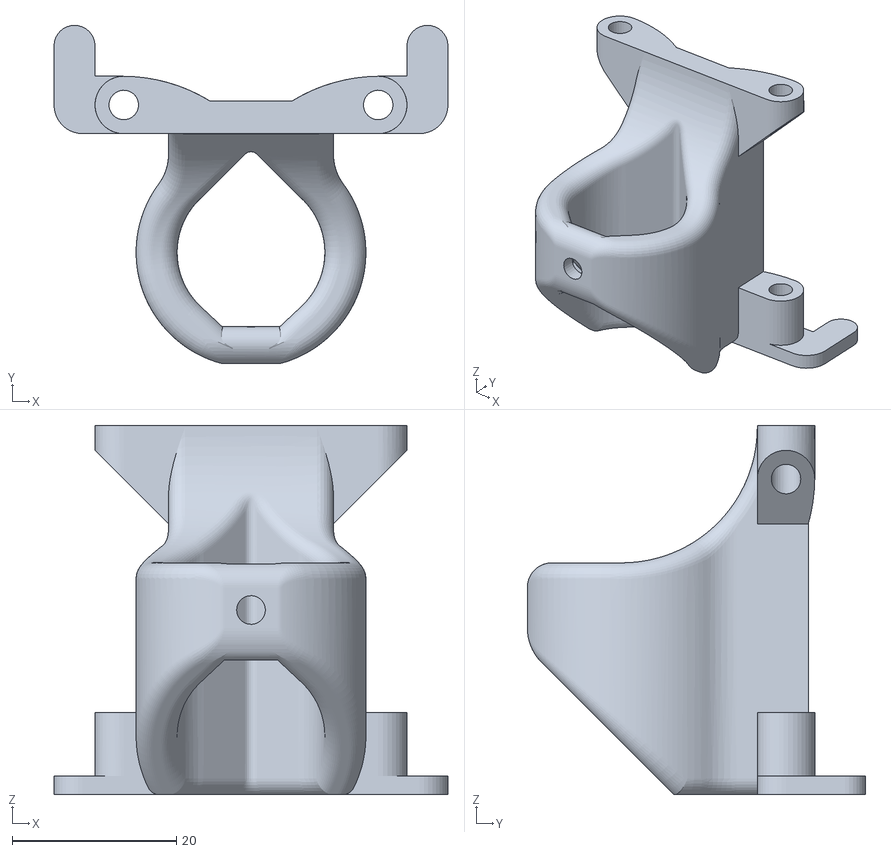
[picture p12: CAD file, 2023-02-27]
files/Carro Z/Imprimir si o si/pen_v_mount.stl
48.0 x 41.2 x 45.0

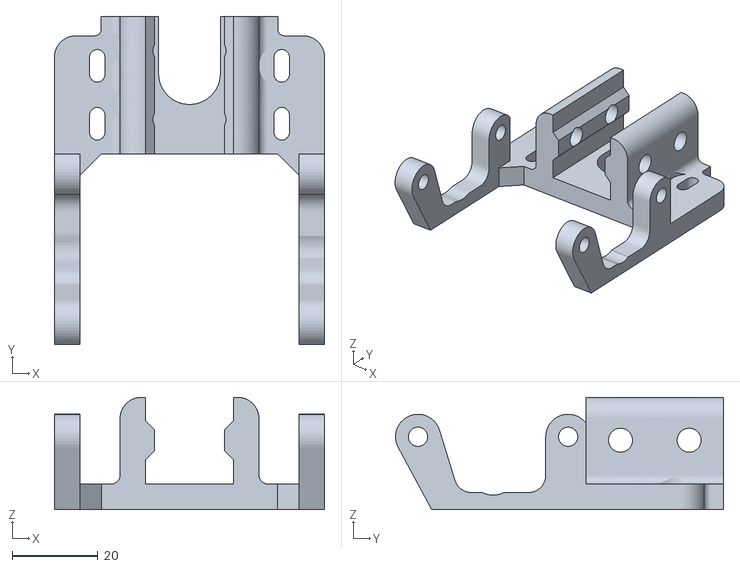
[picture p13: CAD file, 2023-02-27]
files/Carro Z/z_mount_28byj-48_v2020.stl
63.0 x 76.4 x 26.2

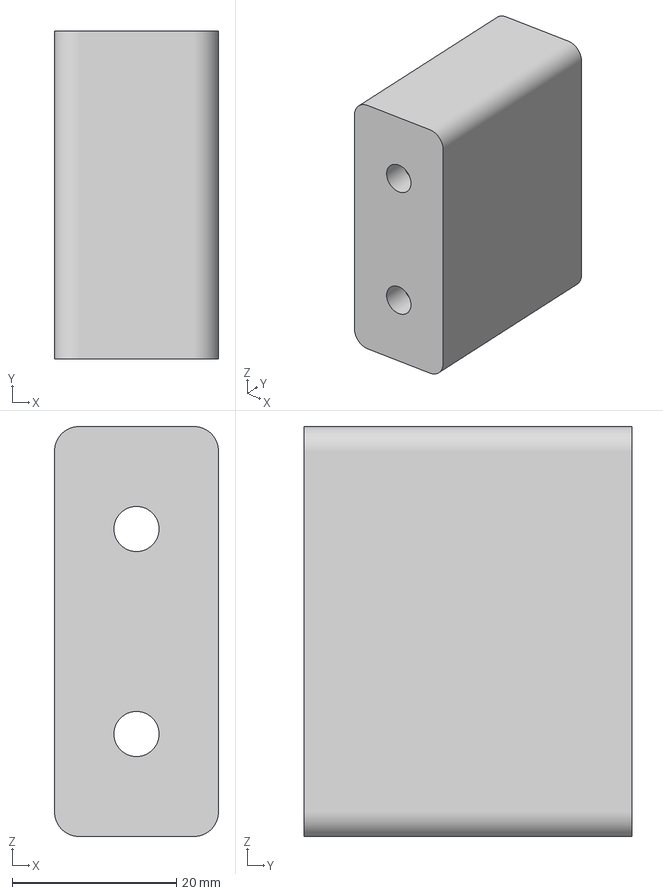
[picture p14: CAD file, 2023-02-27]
files/Patas-imprimir 4.3mf
20.0 x 40.0 x 50.0 mm

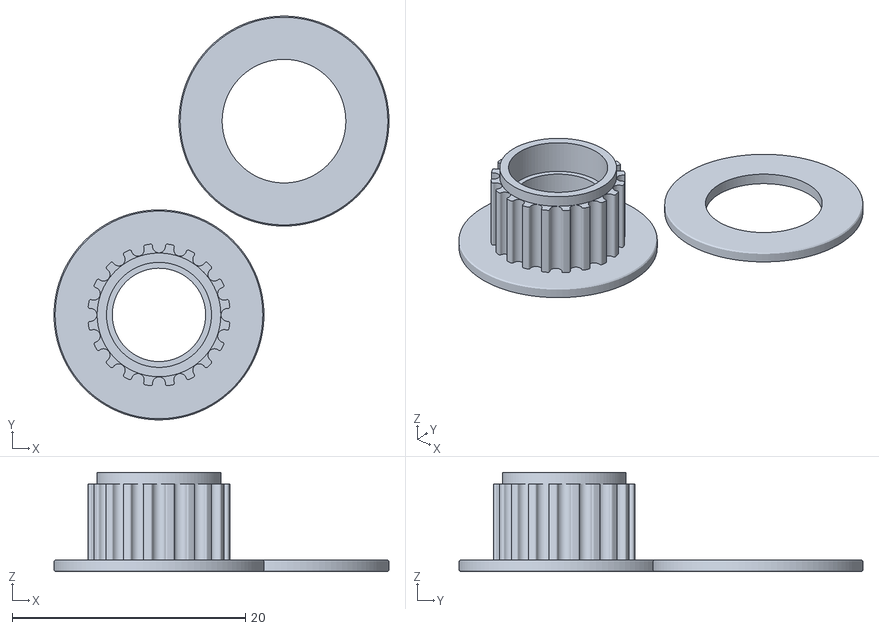
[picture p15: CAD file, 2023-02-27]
files/Poleas/gt2_20t_pulley_dzino_3dprint12.stl
28.7 x 34.6 x 8.50

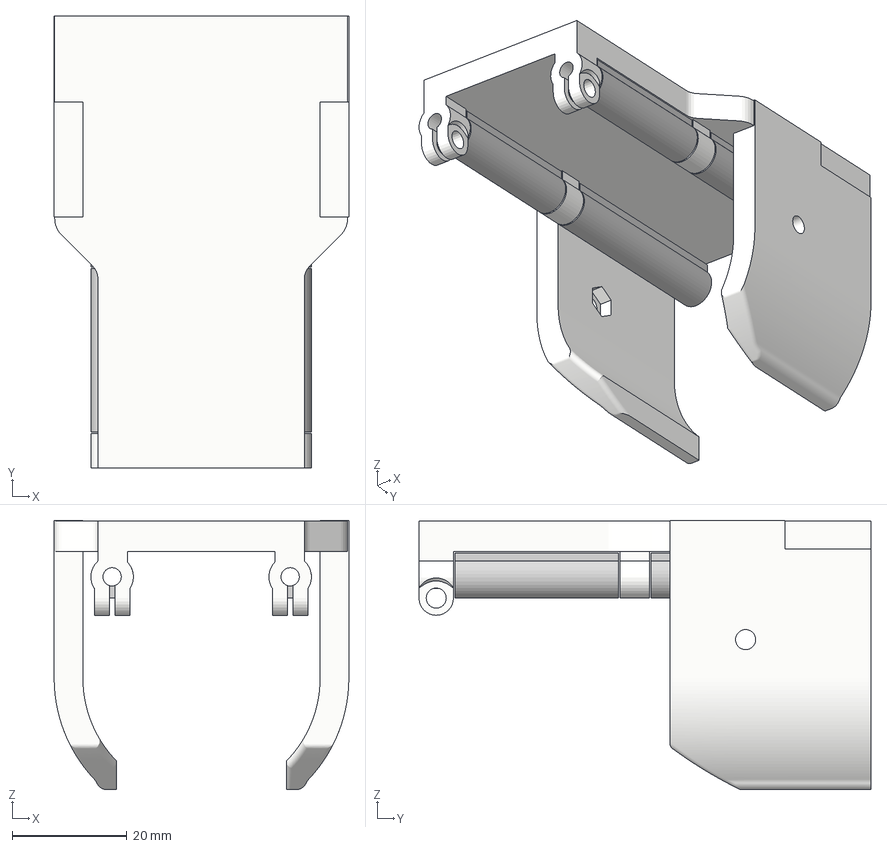
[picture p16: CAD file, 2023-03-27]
files/Z Dario/Pen Holder nuevo/base_slide_mount_short con soportes.3mf
51.3 x 78.7 x 46.9 mm
base_slide_mount_short
soportes base_slide (1)
soportes base_slide (2)
soportes base_slide (3)
soportes base_slide

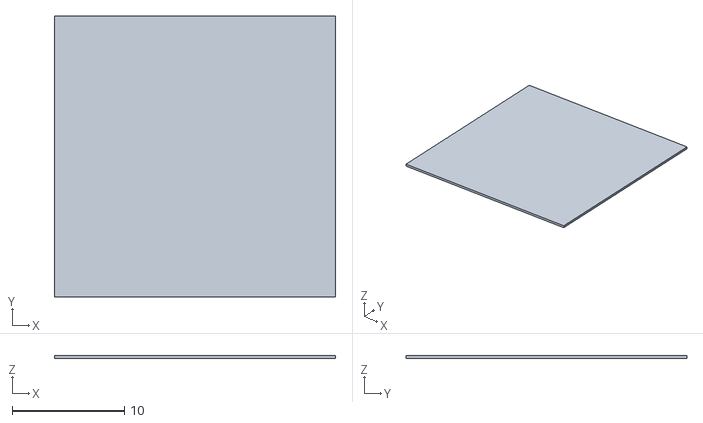
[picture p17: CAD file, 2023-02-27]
testcube_25mm(2)(2)(3).stl
25.0 x 25.0 x 0.28

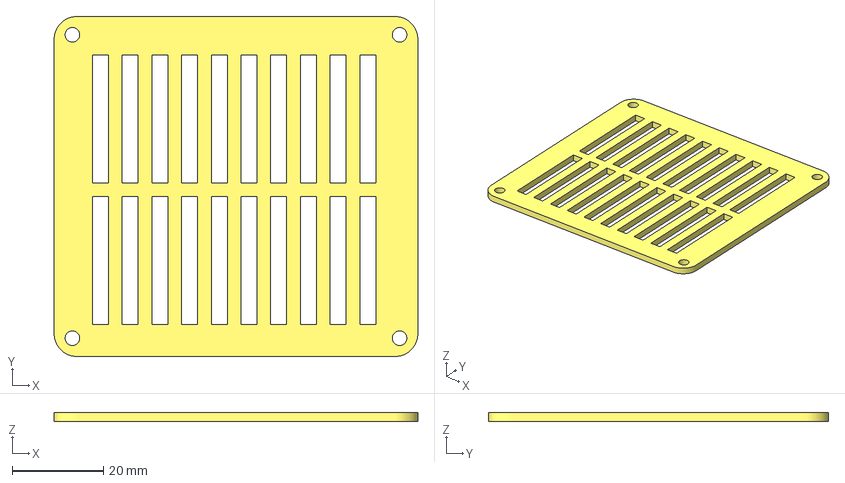
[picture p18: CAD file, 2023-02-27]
files/Arduino CNC Case/DC/Case Tapa.3mf
79.6 x 74.4 x 2.00 mm

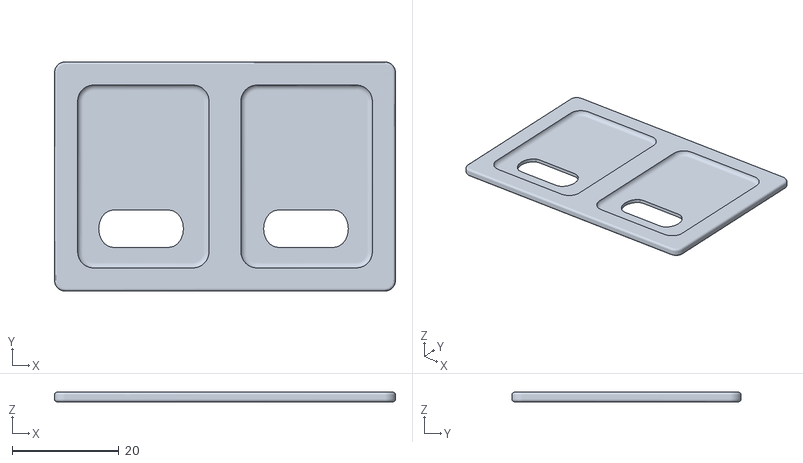
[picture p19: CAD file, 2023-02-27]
files/Arduino CNC Case/UnoCNC_BackPanel.stl
64.0 x 43.0 x 1.80

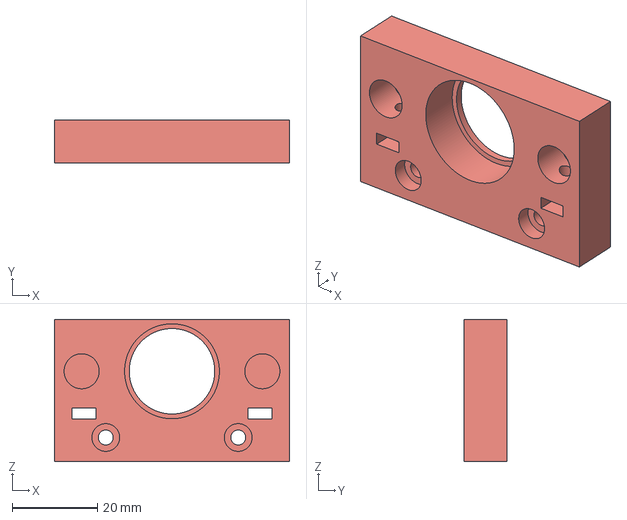
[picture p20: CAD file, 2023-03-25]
files/Carro Z/carro Z DC/Base.3mf
55.0 x 10.0 x 33.3 mm

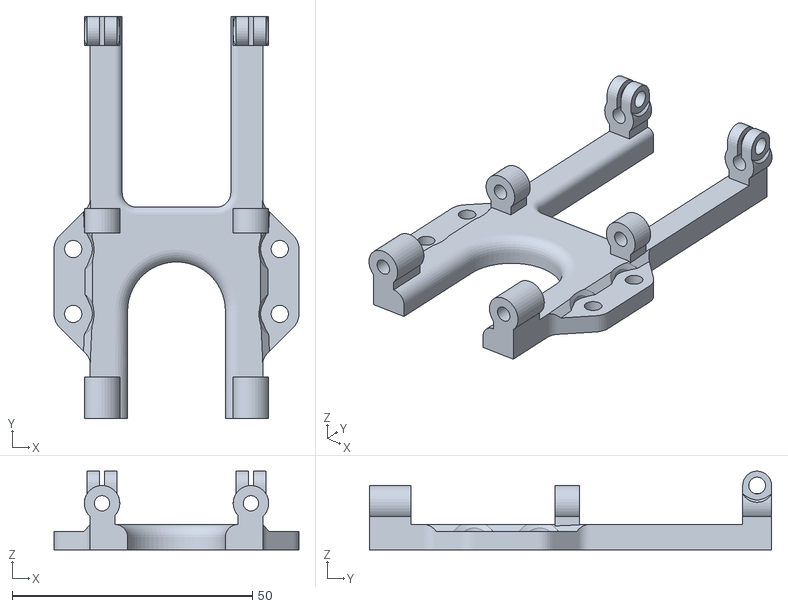
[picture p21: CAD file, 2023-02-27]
files/Carro Z/Imprimir si o si/base_slide_mount_long.stl
51.0 x 83.7 x 16.4

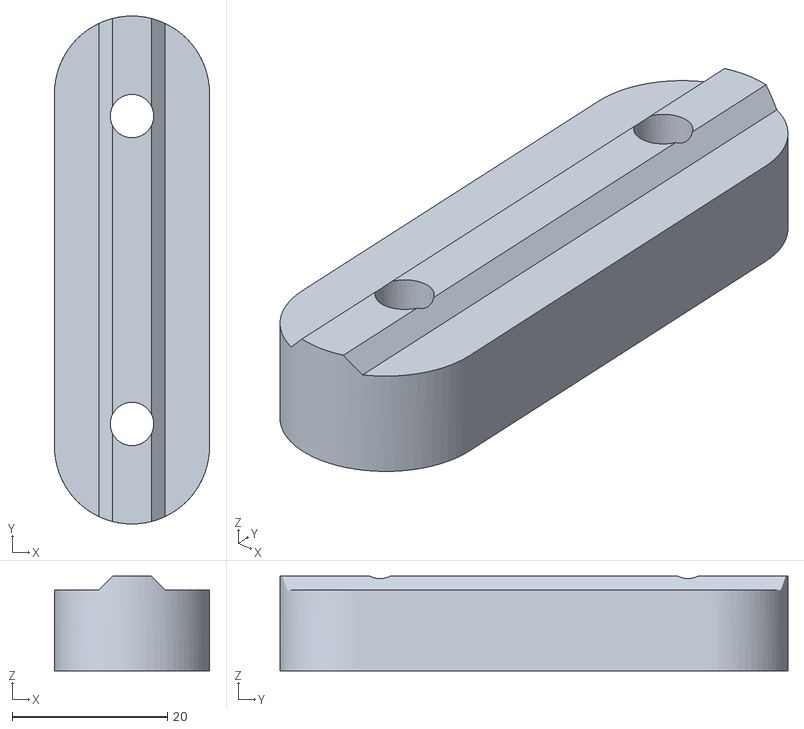
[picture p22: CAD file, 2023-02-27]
files/Carro Z/v2020_z_10_4mmshim_plate.stl
20.0 x 65.5 x 12.2

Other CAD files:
files/Poleas/gt2_pulley_dzino3d_print.stl
files/V-Slot Gantry Plate 20mm.step
files/Z Dario/Pen Holder nuevo/pen_v_mount con soportes.3mf
files/Arduino CNC Case/DC/case UNO cnc shield 2040 extrusion.step
files/8x_M5x1mmSpacers.stl
files/8x_M5x2mmSpacers.stl
files/8x_M5x3mmSpacers.stl
files/8x_M5x4mmSpacers.stl
files/Arduino CNC Case/DC/Case Box_Ventilada.3mf
files/Arduino CNC Case/UnoCNC_CaseBottom_w_2020_MountV2.stl
files/Arduino CNC Case/UnoCNC_CaseFront.stl
files/BottomPlate_2040_V821.1.stl
files/CarBeltConnect_M_V821.1.stl
files/CarBeltConnect_V821.1.stl
files/Carro Z/6mmplate_with_beltclamp_v31.stl
files/Carro Z/Imprimir si o si/base_slide_mount_short.stl
files/Carro Z/Imprimir si o si/m3_spacer_v1.stl
files/Carro Z/Imprimir si o si/v2020_z_6_4mmshim_plate.stl
files/Carro Z/Imprimir si o si/z_servo_sidemount_v2020.stl
files/Carro Z/carro Z DC/BackPlate.3mf
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

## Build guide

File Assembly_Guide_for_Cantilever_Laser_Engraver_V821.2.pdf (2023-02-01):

# Assembly Guide for Horizontal/Vertical Cantilever Laser Engraver V821.1

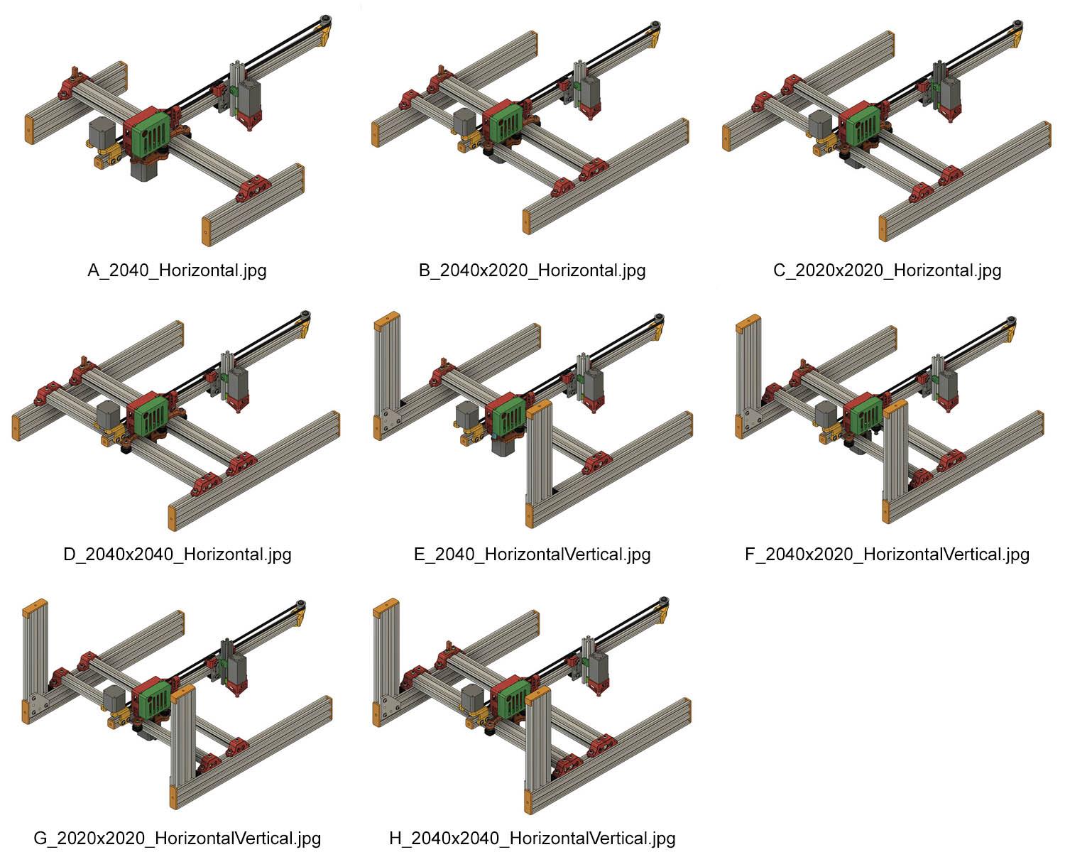
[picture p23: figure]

## Warning:

Be sure to get some good laser safety glasses that protect your eyes against the wave length laser you are using. If using this outside or around other people, make sure you block any stray laser light from their view. The mechanical part of this build is fairly easy, but I found the electronics the most difficult part of this build because of the laser connections. Be sure to understand how to connect your particular laser before attempting this project because you could easily destroy your laser or controller board. Soldering maybe required for the laser wiring depending on your laser & controller board.

This build uses V-Slot aluminum extrusions. Any comment referencing 2020, 2040 or 2060 is assumed to be V-Slot. There are several options for this build now depending on your requirements. I show 8 different configurations in the front page image. Using 2060x500mm for the feet & 2060x250mm for the 90 degree vertical leg will allow you to use this machine in horizontal or vertical mode which to the software you are using will make no difference. This is shown in versions E-G configurations on 1st page. For clarity in this document, I will call the V-Slot 2040 where the main plates are connected the Main Beam & the V-Slot 2020 where the laser rolls back & forth the Cantilever. If you are using either a 2040/2020 or 2020/2020 for double beams, the beam with the bottom motor attached will be called the Main Beam & the other one the Back Beam.

There is also an option to use double V-Slot 2020 to give you more rigidity with smaller printed plated top & bottom plates & 4 - OverHd_2020x2060_Bracket_V821.1.stl (Shown in option C & G). This will allow you to use a longer cantilever. You will also need 4 additional wheels & related hardware & a few more Tee Nuts with M5x12mm screws for the double beams. In vertical mode, a 1000mm V-Slot 2020 will work. You can also use a 2040 from previous build as the main beam going across & add the additional 2020 later. The option I am using is F with a 2040x600mm Main Beam, 2020x600mm Back Beam & a 2020x700mm Cantilever. This gives me a working area of 425mmx425mm (16.7”x16.7”). Using a 2020x600mm Cantilever will give you 305mm (12”). I am using a NEJE 6W laser which weighs 3.6oz.

I am using stainless steel screws & Locknuts, Socket Button Head M5 screws and M3 Socket cap screws. I don’t use the M3 button heads as they take too small of an Allen wrench for my liking. There are no clearance problems with using standard Socket head M5 screws. There are no tapped holes needed in this build as there were before, but you might consider tapping the short Z-axis 2020 and one end of the 2020 cantilever for future use if you are comfortable tapping M5 holes. The short 125mm length of V-Slot 2020 for the Z-axis was cut from a 250mm length with a hack saw. The Z-axis does not have to be a perfect cut on one end, but you might want the top flat if you tap that hole. The controller board I am using is an EleksMaker Mana 3 board, but I have successfully setup an Arduino UNO clone with a CNC Shield V3 and also setup a Keyestudio CNC Shield V4 board. The laser connections are simpler on the EleksMaker board, but the limit switch wiring on that board is not as straight forward. I am not using endstops, but created the mounts for them. The end caps for the V-Slot 2060 & V-Slot 2020 are press fit, so not additional hardware needed for them.

The offset of the cantilever V-Slot 2020 can easily be adjusted after the build by loosening 3 - M5 screws attached to Tee Nuts below the V-Slot 2020 (4 screws if using 2020/2020 (C or G), 2040/2020 (B or F) or 2040x2040 (D or H) beam option). This will allow you to find a happy medium between counterbalance & burning width.

Before starting this build you should also consider which axis you want to use for X and Y. I initially wanted my X-axis to be along the Main Beam & Y along the Cantilever. If you are planning to use the rotary turntable (https://www.thingiverse.com/thing:4958047), you might want to consider using the Cantilever as the X-Axis since the Lightburn currently does not have a way to use Y-axis for what they call the “scanning axis” in rotary mode & they say they are not likely to add it.

Below are 2 images that show how the X and Y axis look in either configuration. The Red line denotes the X-Axis & the Green line denotes the Y-axis If you are using the Cantilever axis as the X-axis as shown in 2nd image, you might consider using the mirrored motor & idler mount, (MotorMount_Above_M_V821.stl & IdlerMount_Above_M_V821.stl). This would allow you to move the laser carriage to the opposite side of the cantilever.

Below is a chart of the 3D printed parts info for 1st version (A) in image from front page. My total print time was less than 17 hours & used 7.5oz of filament. Total weight of my machine should be from 6lbs 5oz – 12lbs.

File Name | Print Time | Weight(oz) | Perimeters | Infill %
BottomPlate_V821.1.stl | 2:25:00 | 1.37 | 8 | 80%
TopPlate_V821.1.stl | 1:30:00 | 0.85 | 8 | 80%
M5x29_2_Standoff.stl | 0:19:00 | 0.08 | 3 | 20%
MotorMount_Above_V821.stl | 1:42:00 | 1.1 | 8 | 80%
IdlerMount_Above_V821.stl | 1:04:00 | 0.43 | 8 | 80%
CarBeltConnect_V821.1.stl | 0:20:00 | 0.13 | 6 | 60%
CarBeltConnect_V821.1_M.stl | 0:20:00 | 0.13 | 6 | 60%
LE_Z_TopSlider_V2017.stl | 0:32:00 | 0.19 | 3 | 20%
LE_Z_BotSlider_V2017.stl | 0:09:00 | 0.04 | 3 | 20%
Shim_Plate_6_4mm_V821.stl | 0:37:00 | 0.25 | 6 | 60%
LaserAirAssist_V4.stl | | | 3
LaserAirAssist_V4_M.stl (or Mirrored) | 1:16:00 | 0.35 | 3 | 20%
Laser_focus_Wheel.stl | 0:07:00 | 0.03 | 3 | 20%
Y-Axis_Mech_LS_Bracket_V821.stl | 0:21:00 | 0.15 | 3 | 20%
X-Axis_Mech_LS_Bracket_V821.stl | 0:35:00 | 0.15 | 3 | 20%
OverHd_2040x2060_Bracket_V821.stl | 1:43:00 | 0.7 | 8 | 80%
OverHd_2040x2060_Bracket_V821.stl | 1:43:00 | 0.7 | 8 | 80%
X_LS_Stop_V821.stl | 0:16:00 | 0.12 | 6 | 60%
V2060_EndCap.stl | 0:27:00 | 0.17 | 3 | 20%
V2060_EndCap.stl | 0:27:00 | 0.17 | 3 | 20%
V2060_EndCap.stl | 0:27:00 | 0.17 | 3 | 20%
V2060_EndCap.stl | 0:27:00 | 0.17 | 3 | 20%
V2020_EndCap.stl | 0:12:00 | 0.05 | 3 | 20%
Total | 16:59:00 | 7.5
Bill of Materials is in the file:

Cantilevered_LaserEngraver_V821.1_BOM.xlsx

The BOM has a different TAB for each configuration.
With all the different configurations, I may not have the basic hardware count correct, so I would order a couple of extra screws & Tee Nuts to be sure you have enough. Some of the brackets you buy might need a spacer for the M5 screw & Tee Nut to fit correctly. There are several Spacers included in 3d printed parts.

Build log for this started in July of 2020. Link to that log is here:

https://forum.v1engineering.com/t/cantilevered-laser-engraver/19179

Another build log with duplicate & some different info can be found here:

Horizontal Cantilever or Vertical Diode Laser Engraver | OpenBuilds (https://openbuilds.com/builds/horizontal-cantilever-or-vertical-diode-laser-engraver.10031/)

Design files: https://www.thingiverse.com/thing:4934772

Optional Turntable Design files: https://www.thingiverse.com/thing:4958047

## Start off with the Main Plate Assembly

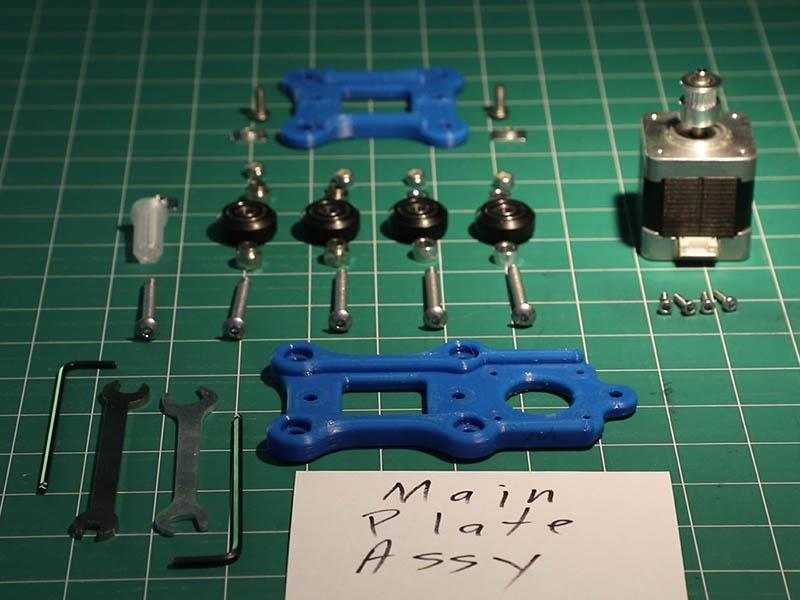
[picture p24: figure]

## Need 3 Printed Parts for this Assembly (Same or Similar for all configurations)

BottomPlate_V821.stl or (BottomPlate_2020_V821.stl for double 2020 Beam Options C or G) TopPlate_V821.stl or TopPlate_2020_V821.stl for double 2020 Beam Options C or G) M5x29_2_Standoff.stl or (M5x23_Standoff.stl for double Beam Options B, C, D, F, G or H)
4 – M3x10mm screws for Nema17 motor mount
5 – M5x40mm socket head screws for wheels & back standoff (1 screw used later)
4 – M5 Locknuts
2 – M5x12mm screws for V-Slot 2020 Tee Nut mount
3 – M5 Tee Nuts (1 Tee Nut used later)
4 – 6mm spacers
4 – Eccentric spacers
4 – V-Wheels with bearings
1 – Nema 17 motor
1 – 20T timing pulley (need 20T instead of 16T since the Cantilever arm needs a wider belt width for better clearance)
Allen wrench for M3 & M5 screws & wrench for Locknuts & adjusting Eccentric spacers

Attach the 20T timing pulley to Nema 17 motor with grub screws. Use a 6mm Allen wrench to space bottom of the pulley to bottom of motor. Tighten screws just enough to keep it in place as it might need a little adjusting once attached to the V-Slot 2040 beam.

Attach the Nema 17 motor to the bottom plate 1st using the 4 – M3x10mm screws. My motor is 42mm deep. A shorter 34mm deep motor will work & pancake 22mm deep motors might work, but I would not go any deeper than 42mm as you might have clearance problems. Note the location of wire connection for motor on 2nd photo.

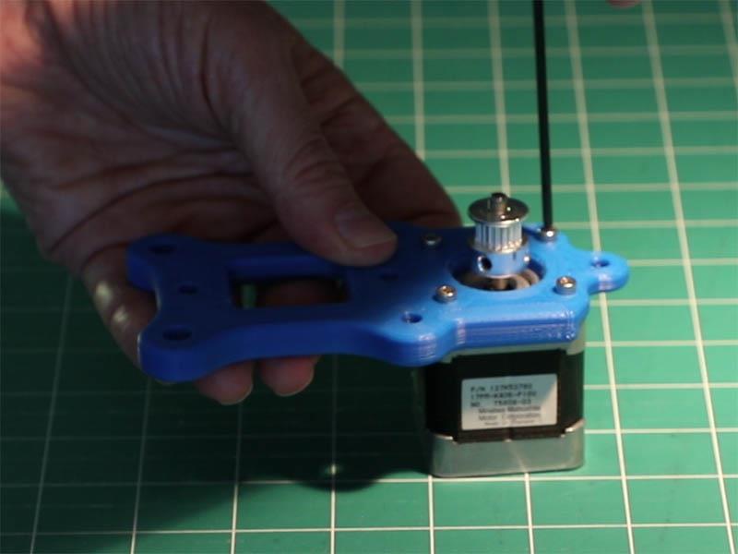
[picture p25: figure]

Next attach the 2 – M5x12mm & Tee Nuts to top plate as shown below.

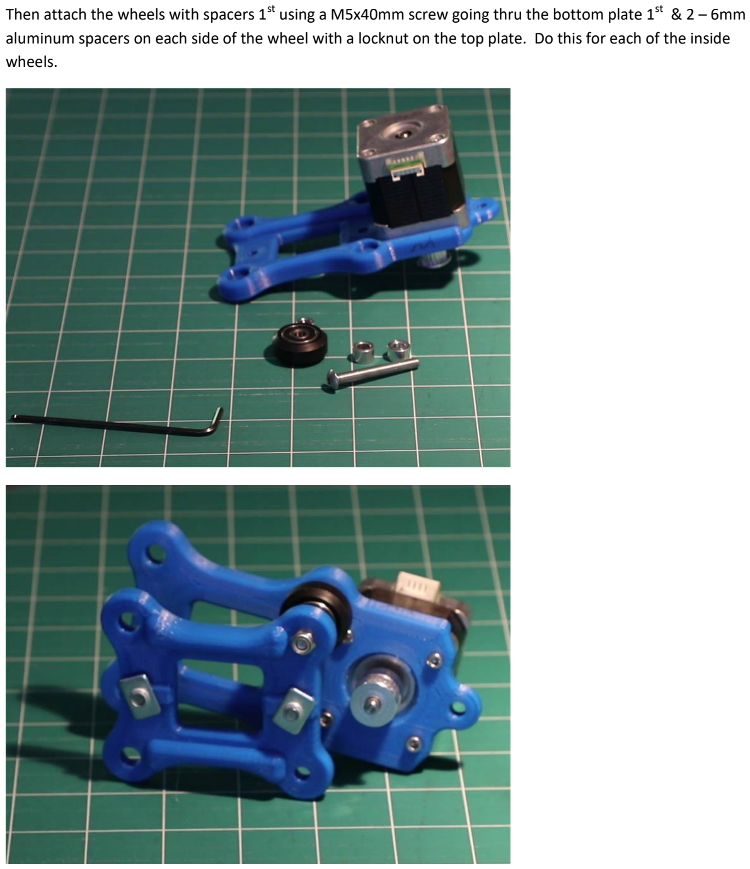
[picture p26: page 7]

Then attach the wheels with spacers 1st using a M5x40mm screw going thru the bottom plate 1st
& 2 – 6mm
aluminum spacers on each side of the wheel with a locknut on the top plate. Do this for each of the inside wheels.

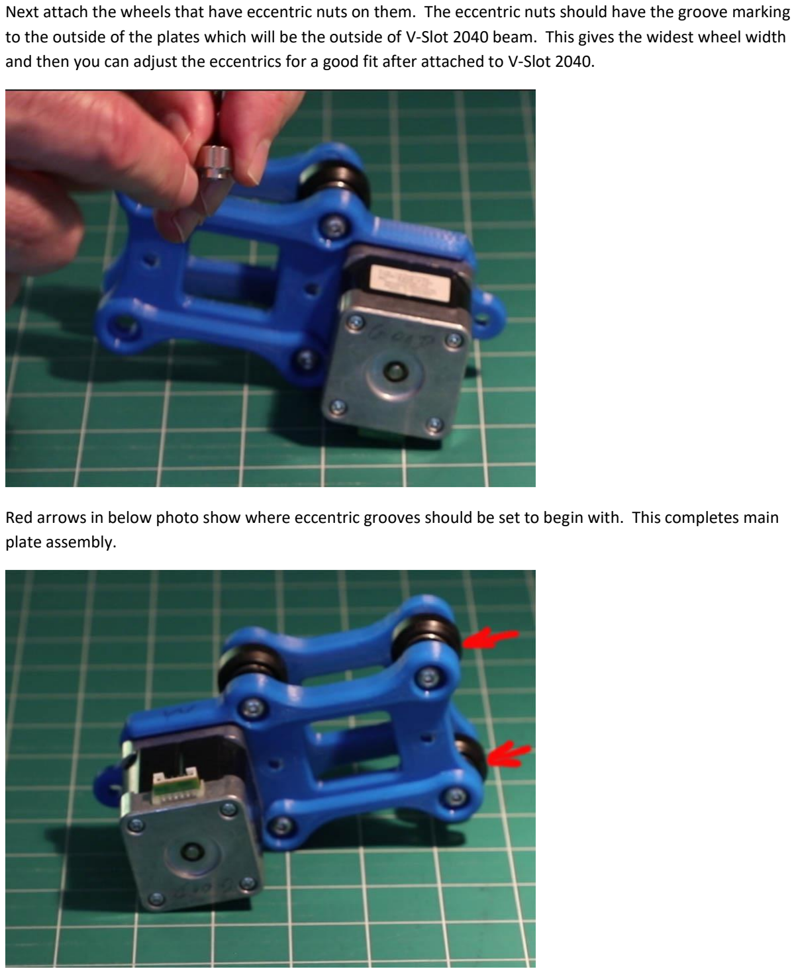
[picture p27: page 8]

Next attach the wheels that have eccentric nuts on them. The eccentric nuts should have the groove marking to the outside of the plates which will be the outside of V-Slot 2040 beam. This gives the widest wheel width and then you can adjust the eccentrics for a good fit after attached to V-Slot 2040.

Red arrows in below photo show where eccentric grooves should be set to begin with. This completes main plate assembly.

## V-Slot 2020 Carriage Assembly

3 – Printed parts, CarBeltConnect_V821.1.stl, CarBeltConnect_V821.1_M.stl, Shim_Plate_6_4mm_V821.stl 1 - Gantry Plate for V-Slot 2020
1 – V-Slot 2020x125mm aluminum extrusion
4 – M5x30mm screws for wheels
2 – 6mm aluminum spacers
2 – Eccentric spacers
4 – V-Wheels with bearings.
8 – 10x5x1mm shims
2 – 3mm aluminum spacers
4 – M5 Locknuts
2 – M5x16mm screws (mounts Shim plate to V-Slot 2020) 2 – M5 Tee Nuts
2 – M3x12mm screws (Carriage Belt clamp mount)
2 – M3 locknuts
Tools, Allen wrenches & wrenches for locknuts & eccentric spacers.

Attach CarBeltConnect_V821.1.stl & CarBeltConnect_V821.1_M.stl to Gantry plate with 2 - M3x12mm screws & leave the 2 – M5 holes lined up to install wheel screws. There are 2 holes for M3 screws, but one is all that is needed on each side since the M5 wheel screws will hold it further in place & keep it from twisting.

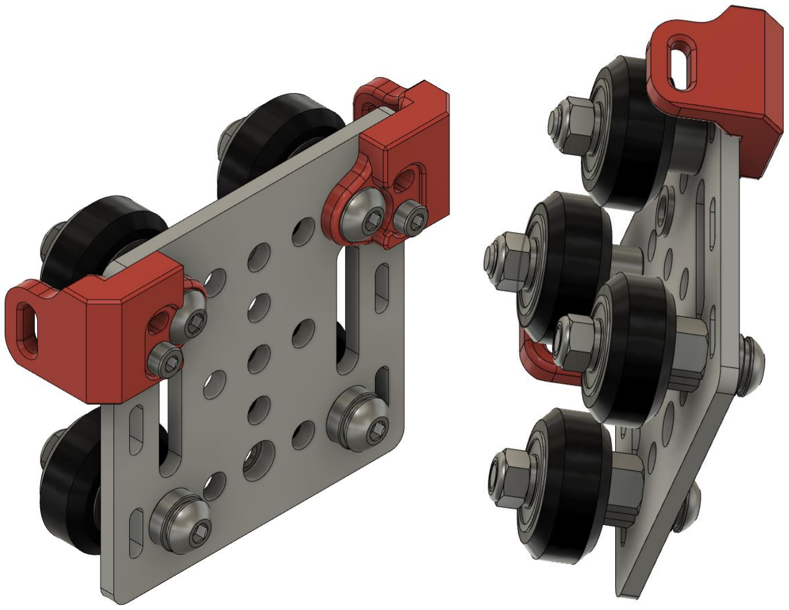
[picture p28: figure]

Bottom wheels with eccentrics have a 1mm & 3mm thick washer to balance out the carriage belt clamps at the top. Optionally, you can substitute 8x_M5x4mmSpacers.stl plastic spacers instead of those. Top wheels have a M5x30mm screw going thru the plastic belt clamps with 6mm aluminum spacer on the plate side of the wheel with a 1mm spacer & locknut on the other side of wheel. The bottom wheels have a M5x30mm screw with a 1mm & 3mm spacer (optional 8x_M5x4mmSpacers.stl) then thru the plate with an eccentric nut, the wheel with a spacer & locknut. Note the initial location of the notch in the eccentric nuts.

Attach the 2 – M5x16mm screws with 1mm spacers, Shim_Plate_6_4mm_V821.stl & Tee Nuts as shown in below image. Tee Nuts should be loose.

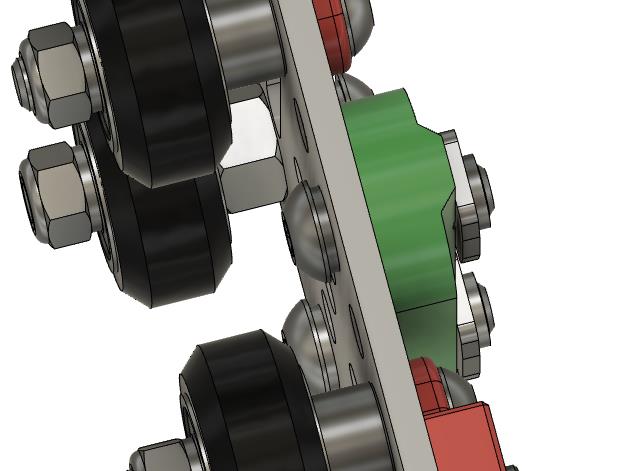
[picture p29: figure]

If you familiar with tapping M5 thread holes, consider tapping the top of the short Z-axis hole for future use. I am using that to attach a 10” paper plate to block laser light from that side when burning in vertical mode outside.

Slide the short V-Slot 2020 for the Z-Axis into place as shown in photo below. I have the V-Slot 2020 positioned about 14mm below the bottom of the Gantry plate, but is easily adjusted later by loosening those 2 – M5x16mm screws. Below is what this assembly looks like.

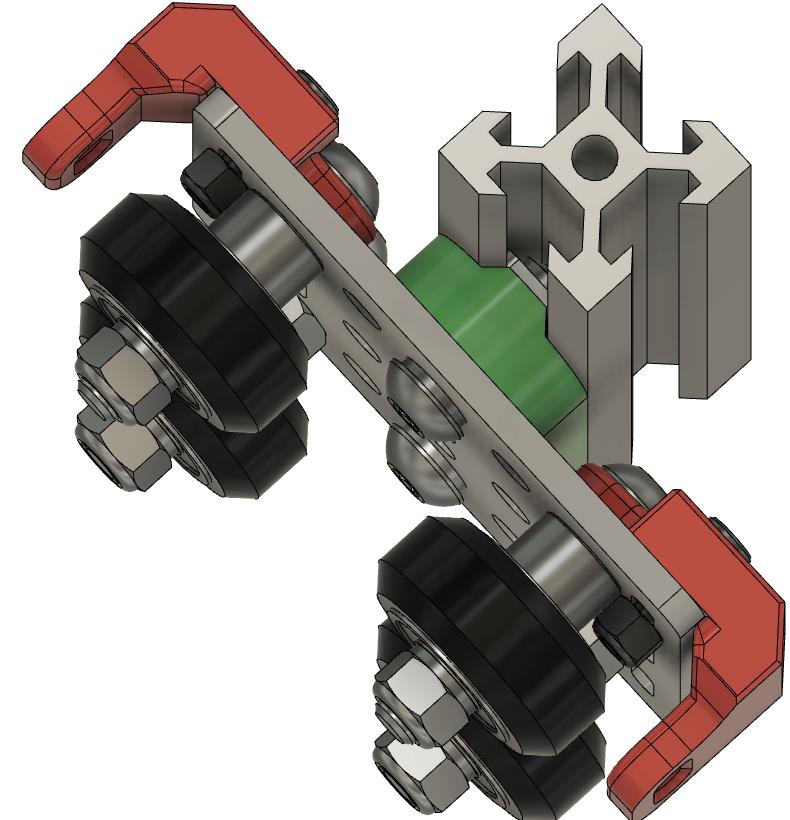
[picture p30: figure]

## Motor and Idler Mounts for Cantilever Beam

2 – Printed parts MotorMount_Above_V821.stl & IdlerMount_Above_V821.stl
(or mirrored versions MotorMount_Above_M_V821.stl & IdlerMount_Above_M_V821.stl) 1 – Nema 17 Motor
1 – 20T timing pulley
1 – Smooth Idler Pulley Kit
4 – M3x10mm screws
5 – M5x12mm screws
5 – M5 Tee Nuts
1 – M5x25mm screw
2 – 1mm aluminum spacers
1 – M5 Locknut
Allen wrenches for M3 & M5 screws & wrench for M5 locknut

Mount 20T timing pulley to motor using a 6mm Allen wrench to adjust the offset of pulley to motor as shown below. Tighten the grub setscrews enough to that shaft with one screw against flat part of shaft if it has one. Do final tighten later when we attach the belt.

Note the location of the Nema 17 wire connection on the flatter side of the plastic mount.

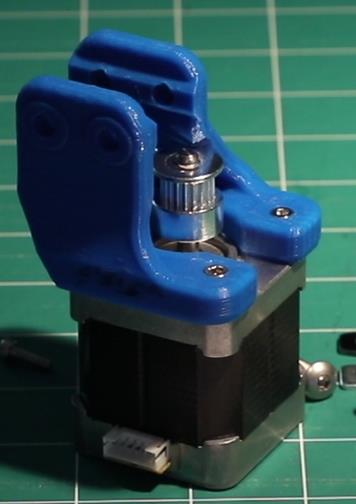
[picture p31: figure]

Tighten the motor to MotorMount_Above_V821.stl (or MotorMount_Above_M_V821.stl) with the 4 – M3x10mm screws & add the 4 – M5x12mm screws with M5 Tee Nuts to the Plastic mount as shown in the image below. Put this part aside.

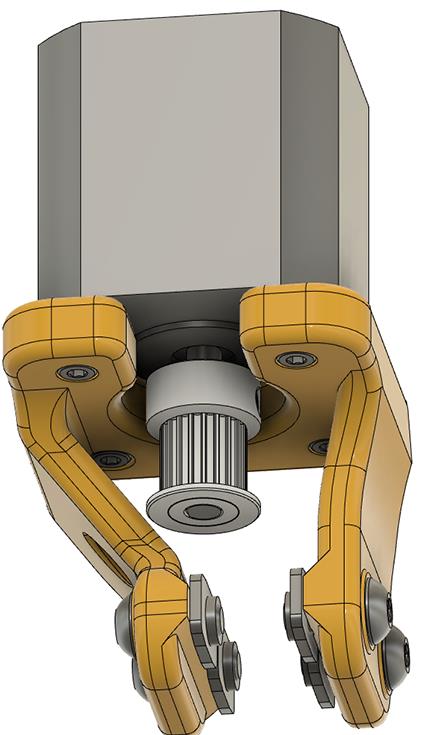
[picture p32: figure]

## Idler Mount Assembly

As shown in image below, add an M5x12mm screw with M5 Tee Nut to IdlerMount_Above_V821.stl (or IdlerMount_Above_M_V821.stl if you are orienting laser on other side of cantilever).

Add a M5x25mm screw thru plastic part with 1mm spacer on each side of idler pulley assembly & a M5 locknut on top. Put this part aside.

## Assemble the Main plate assembly with belt to V-Slot 2040 beam with the Two V-Slot 2060 Feet

1. Insert one end of the GT2 belt you cut for the V-Slot 2040 axis with the teeth of the belt against the inside of the V-Slot. Mine is 800mm for a 600mm length of V-Slot 2040.
2. If you are considering making this V-Slot 2040 longer in the future, you could use longer belt.
3. Extend it 20mm or so beyond the end of the V-Slot 2040. Mine extends about 35-40mm on both sides.
4. Take a M5 Tee Nut with the M5x5mm set screw as shown in picture below.
This will be the right side as viewed from the back of the machine.
5. Insert the Tee Nut at that end & tighten the set screw against the belt.
6. If you are using a M5 screw instead of a set screw, you will not be able to have the Tee Nut at the end as it will hit the plastic part OverHd_2040x2060_Bracket_V821.stl or OverHd_2020x2060_Bracket_V821.1.stl if you are using the double V-Slot 2020 configuration.

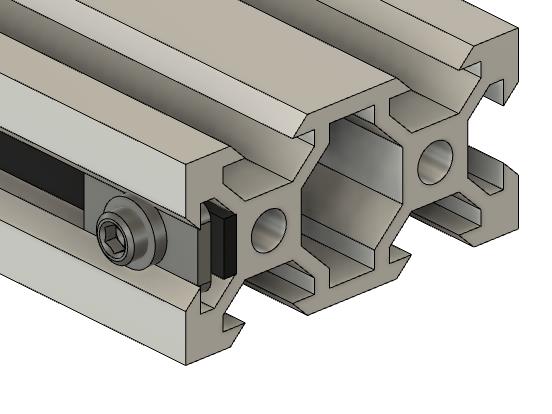
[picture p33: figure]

7. Slide the Main Plate assembly onto the V-Slot 2040 from the opposite side with the belt resting against the inside of the V-Slot 2040 extrusion. This procedure is the same for the 2020 Main Beam if you are using that setup.
8. Let the belt ride against wheels.

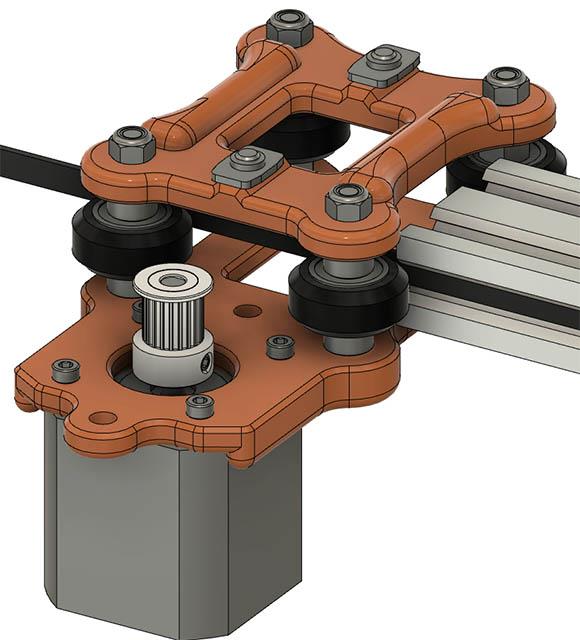
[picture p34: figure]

9. Roll the plate assembly 150mm or so inward to make it easier to attach belt & clamp.

10. Hold the belt on the attached side of the carriage assembly & push the unattached side until you get a loop you can grab and wrap around 20T timing pulley as shown below. You could also use needle nose pliers to pull it from the V-Slot groove.
11. Add the M5 Tee Nut & M5x5mm setscrew to the other end.
12. Pull on unattached end of belt & tighten the set screw. You should have some belt extended beyond Tee Nut. I would leave a little belt extended beyond Tee Nut in case you need to take apart again.

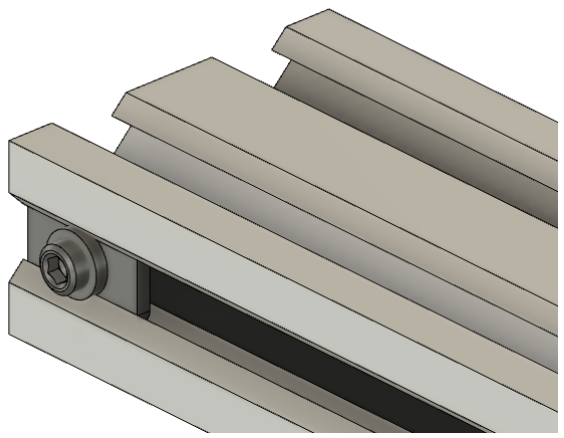
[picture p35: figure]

## Add the V-Slot 2060x250mm feet to each end

1. An OverHd_2040x2060_Bracket_V821.stl (OverHd_2020x2060_Bracket_V821.1.stl for 2020 Main Beam) printed part is used on both feet.
2. Using 4 – M5x12mm screws with Tee Nuts attach the side shown or 3-M5x12 screws with Tee Nuts for 2020 Main Beam.
3. Slide Tee Nuts into appropriate slots as shown before attaching plastic part.
4. Note the orientation of where the belt is in photo as the other side has an additional part.
5. Push the V-Slot 2040 or 2020 all the way into the plastic part.
6. Line up each Tee Nut as you tighten down each of the M5x12mm screws.
7. The plastic part is shown slightly transparent in picture for clarity.

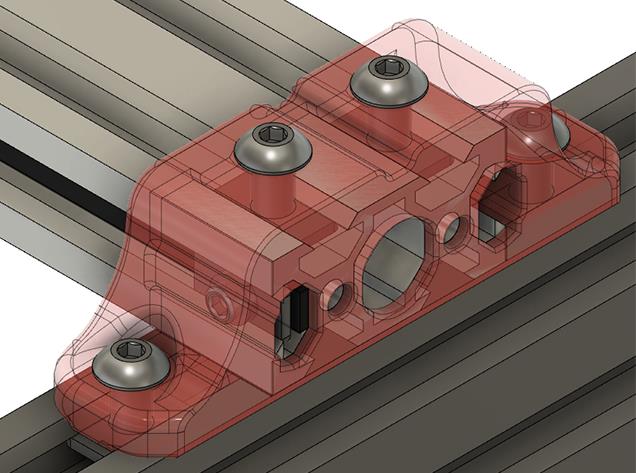
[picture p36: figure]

8. Other side has the printed parts X_LS_Stop_V821.stl & OverHd_2040x2060_Bracket_V821.stl. If you are not using end stops, you can connect this part like the other side.

### 9. Use 2 – M5x12mm screws with Tee Nuts on V-Slot 2060 connection 10. Place the X_LS_Stop_V821.stl part with slotted holes on top of the

OverHd_2040x2060_Bracket_V821.stl
11. Use 2 - M5x16mm screws with Tee Nuts to attach the bracket to the V-Slot 2040 beam.
12. Make sure the V-Slot 2040 is all the way in the bracket & tighten all the screws.

13. If you are not creating a vertical configuration, you can now press fit the 4 - V2060_EndCap.stl into the ends of the V-Slot 2060 feet. If you are doing a vertical configuration, you will later need to add some Tee Nuts.

Assemble the Cantilever V-Slot 2020 and related parts.

### 1. For Single Beam configuration A, B, C or D 2. Attach an M5-40mm screw from hole in back of bottom plate, add M5x29_2_Standoff.stl

plastic part (Light blue in picture) on top of bottom plate with Tee Nut on top.
3. Loosen the 3 – M5 Tee Nuts enough to slide 2020 cantilever on.
4. Slide the Cantilever on as shown below until all 3 Tee Nuts are in. It can also be slid in from the other way if you prefer.
5. My setup has about 158mm of the 2020 extended from the back of the 2040 beam.
6. You can easily adjust this to meet your needs after it is all together by just loosening these same 3 screws attached to the Tee Nuts.

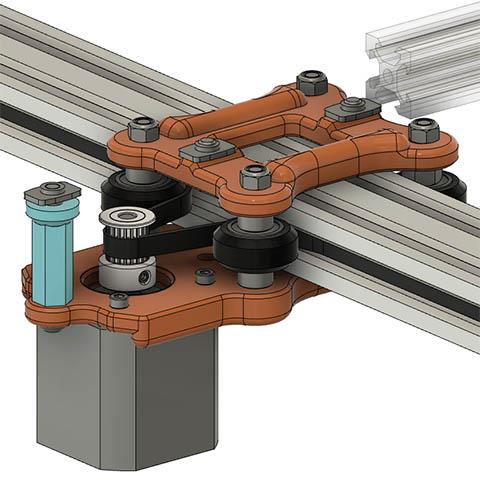
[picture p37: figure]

### 7. If using a 2020 or 2040 Back Beam, attach an M5-40mm screw from hole in back of bottom

plate, add the M5x23_Standoff.stl plastic part between the bottom plate & back top plate with a Tee Nut circled in red. Note Eccentric nuts are on outside for easier adjustment.
8. Loosen the 4 – M5 Tee Nuts enough to slide 2020 cantilever on.
9. Slide the Cantilever on as shown below until all 4 Tee Nuts are in. It can also be slid in from the other way if you prefer.
10. Tighten Tee Nuts in place, but not really tight as you might want to adjust the offset of the cantilever later.

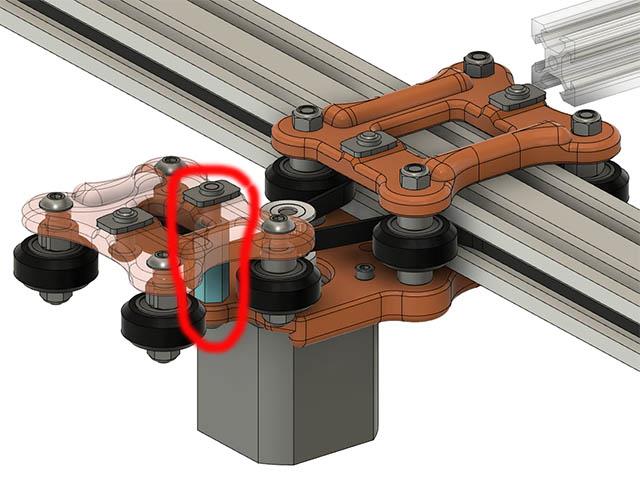
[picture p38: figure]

11. If using double beam, slide the back beam onto the back carriage & tighten eccentric nuts as needed.
12. Loosen the Tee Nuts that hold the Main Beam to each of 2060 feet.
13. Slide this carriage all the way to end & attach the OverHd_2020x2060_Bracket_V821.1.stl or OverHd_2040x2060_Bracket_V821.stl as shown in photo below. Photo shows using 2040 for both the Main & Back Beam and only used one screw & Tee Nut to secure the top of Back 2040.
14. Tighten all the Tee Nut screws.

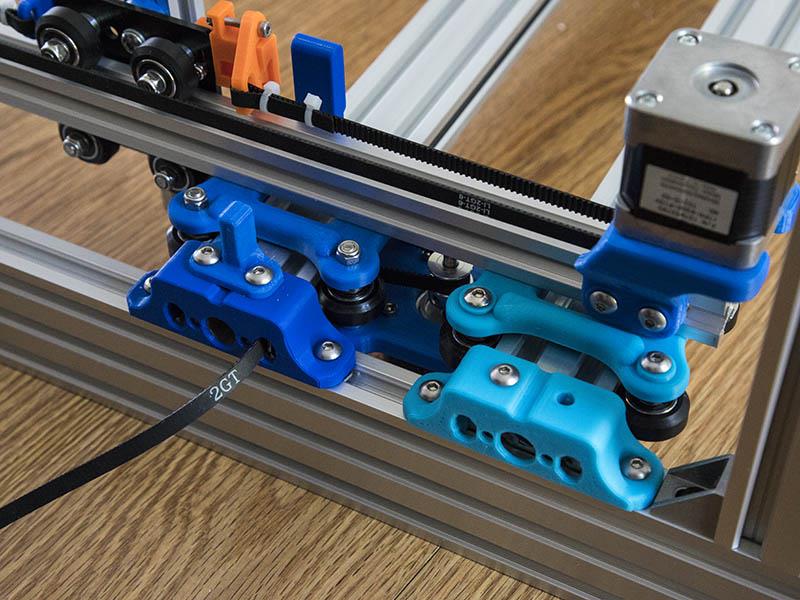
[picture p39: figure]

### 15. Now slide the carriage all the way to the other end and attach the same brackets with

hardware on opposite side.
16. Tighten all the Tee Nut screws on this side.
17. This should insure that the beams are parallel.

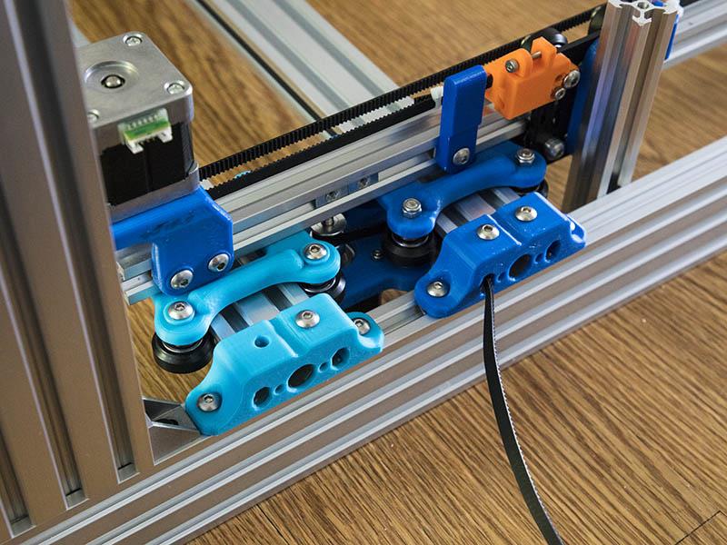
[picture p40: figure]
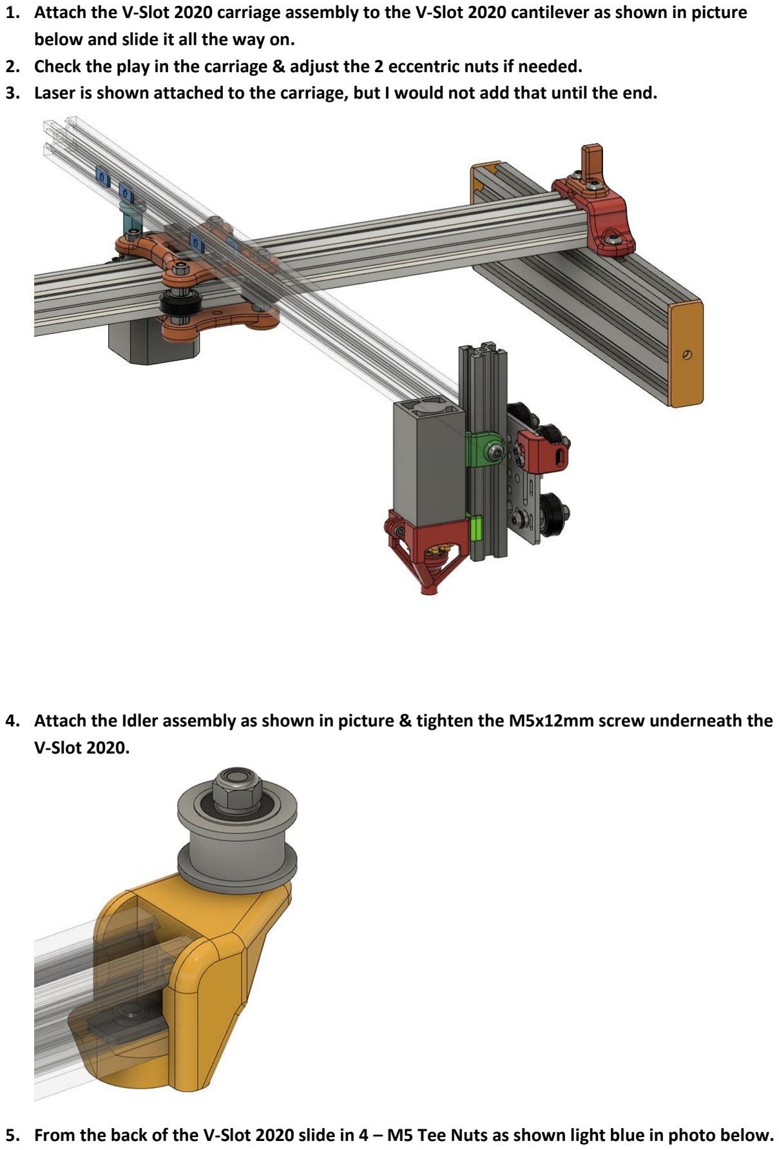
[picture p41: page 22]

1. Attach the V-Slot 2020 carriage assembly to the V-Slot 2020 cantilever as shown in picture below and slide it all the way on.
2. Check the play in the carriage & adjust the 2 eccentric nuts if needed.
3. Laser is shown attached to the carriage, but I would not add that until the end.
4. Attach the Idler assembly as shown in picture & tighten the M5x12mm screw underneath the V-Slot 2020.
5. From the back of the V-Slot 2020 slide in 4 – M5 Tee Nuts as shown light blue in photo below.

6. The back 2 Tee Nuts on one side are for attaching the controller board mount.
7. The other 2 Tee Nuts are for the X & Y Mechanical limit switch brackets.
8. These need to be added before attaching the motor mount in the rear.
9. Attach the motor from the back of the V-Slot 2020 cantilever as shown in photo.
10. It will probably be easier to take the 4 – Tee Nuts off & slide them in as it is sometimes difficult to line up 2 Tee Nuts at a time.
11. Leave a little room at back of V-Slot 2020 to allow for moving the motor back during belt tightening process.
12. Also the V-Slot 2020 endcap extends 12mm into V-Slot 2020 side grooves, so allow clearance for that also.
13. Tighten up 1 Tee Nut screw on each side for now.

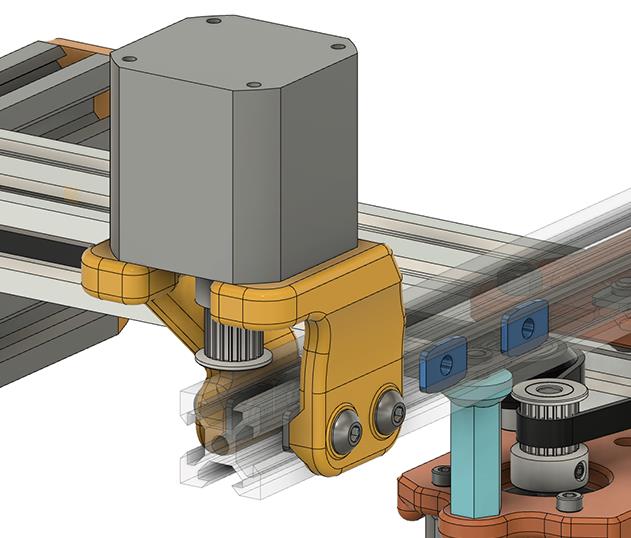
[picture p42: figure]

14. Get the belt you cut for your cantilever axis. The length I used for my configuration is 1270mm with the 600mm V-Slot 2020 extrusion.

15. Attach it to the outside belt clamp on the carriage first. You want this overlapped part to be as short as possible & still have a good connection. Mine extends about 20mm. You can always cut this shorter after it is clamped. Use 1 or 2 wire ties to clamp the belt overlap.

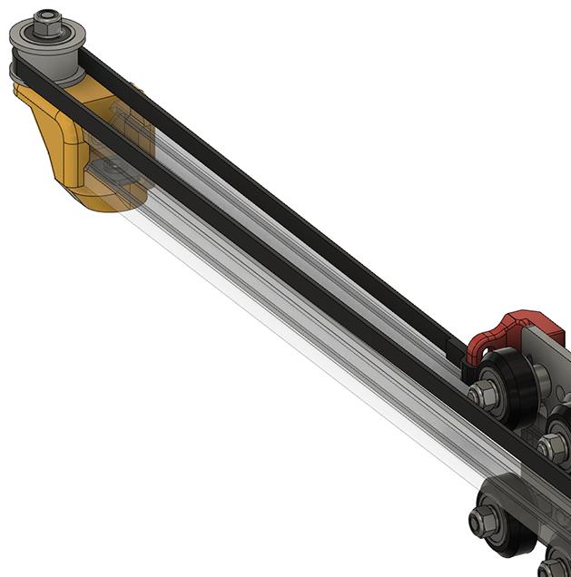
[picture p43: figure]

16. Wrap the belt around the Idler pulley at the end & then thread it thru the Motor Timing pulley at the back & attach the other end of the belt to the inside belt clamp on the V-Slot 2020 carriage as shown in picture below. Tighten as tight as possible. We will tighten it further after next step.
17. Add V2020_EndCap.stl to back of the V-Slot 2020. Internal 2 connections should be above & below to allow for motor to be pulled back as far as possible if needed.

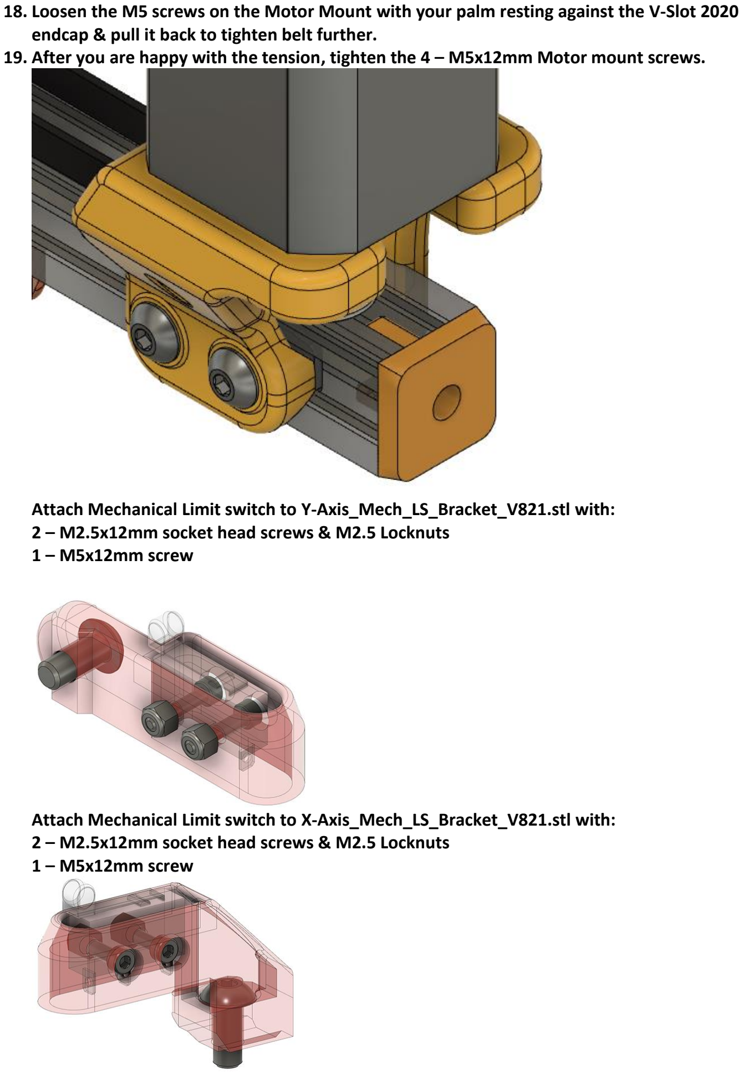
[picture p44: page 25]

18. Loosen the M5 screws on the Motor Mount with your palm resting against the V-Slot 2020 endcap & pull it back to tighten belt further.
19. After you are happy with the tension, tighten the 4 – M5x12mm Motor mount screws.

Attach Mechanical Limit switch to Y-Axis_Mech_LS_Bracket_V821.stl with: 2 – M2.5x12mm socket head screws & M2.5 Locknuts
1 – M5x12mm screw

Attach Mechanical Limit switch to X-Axis_Mech_LS_Bracket_V821.stl with: 2 – M2.5x12mm socket head screws & M2.5 Locknuts
1 – M5x12mm screw

Attach the X-Axis & Y-Axis limit switch assembly to the V-Slot 2020 cantilever as shown in this picture.
Then attach your controller board mount of choice to other 2 Tee Nuts.

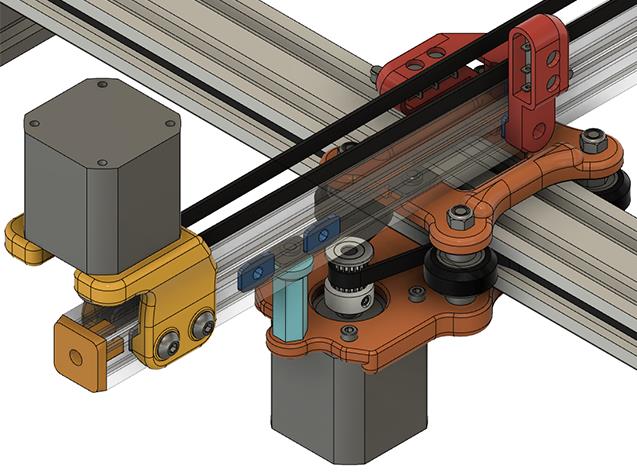
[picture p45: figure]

## Put the Laser Assembly Together Last

Gather the following parts.

1. Printed parts, LE_Z_TopSlider_2020_V821.stl, LZ_Z_BotSlider_2020_V821.stl, Laser_focus_Wheel.stl and LaserAirAssist_V4_M.stl
(LaserAirAssist_V4_M.stl is used instead of other one to allow for most cantilever movement)
2. 5 – M3x10mm screws
3. 1 – M3 Locknut
4. 1 – M5x12mm screw
5. 1 – M5 Tee Nut
6. 1 – Diode Laser (Mine is a NEJE 6W)
7. Add Laser_focus_Wheel.stl to the focus wheel of the laser.
8. Mount LE_Z_TopSlider_2020_V821.stl to top laser threaded holes with the 2 - M3x10 screws.
9. Add the M5x12mm screw and M5 Tee Nut to one side of top slider.
10. Mount LZ_Z_BotSlider_2020_V821.stl and LaserAirAssist_V4.stl to bottom laser threaded holes.
11. Add the M3x10mm screw with locknut to the front bracket on the laser.

12. Mount the Laser Assembly to the V-Slot 2020 Carriage Assembly by sliding the top slider over V-Slot 2020 Z-Axis.
13. Tighten the Laser Assembly to Carriage Assembly with just the 1 M5x12mm screw & Tee Nut
14. You could add a V2020_EndCap.stl to the top of this V-Slot 2020 also, but it is just more weight on the carriage running on the cantilever V-Slot 2020.

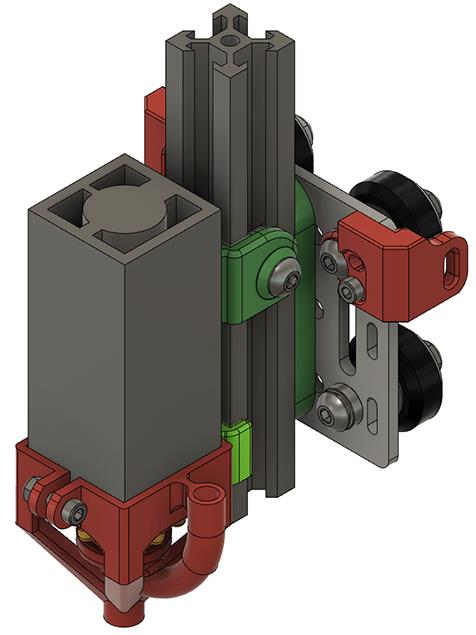
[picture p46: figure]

Check all the screws to make sure they are tight. Adjust the eccentric wheel nuts if needed. Visually check for squareness on the cantilever to the V-Slot 2040 beam.
On a flat surface, check that the height of the cantilever beam is the same height at the V-Slot 2040 beam side as it is at the end where the idler is. If it is not, you might be cantilevering too far. Being slightly off is probably not a problem & you can verify this with your first test burn.

This completes the mechanical build.
You can find additional help with your wiring & troubleshooting from the build log listed at beginning of this guide.

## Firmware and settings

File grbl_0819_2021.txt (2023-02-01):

$0=10 ;Step pulse time, microseconds
$1=255 ;Step idle delay, milliseconds
$2=0 ;Step pulse invert, mask
$3=0 ;Step direction invert, mask
$4=0 ;Invert step enable pin, boolean
$5=0 ;Invert limit pins, boolean
$6=0 ;Invert probe pin, boolean
$10=1 ;Status report options, mask
$11=0.010 ;Junction deviation, millimeters
$12=0.002 ;Arc tolerance, millimeters
$13=0 ;Report in inches, boolean
$20=0 ;Soft limits enable, boolean
$21=0 ;Hard limits enable, boolean
$22=0 ;Homing cycle enable, boolean
$23=0 ;Homing direction invert, mask
$24=25.000 ;Homing locate feed rate, mm/min
$25=500.000 ;Homing search seek rate, mm/min
$26=250 ;Homing switch debounce delay, milliseconds
$27=1.000 ;Homing switch pull-off distance, millimeters
$30=1000 ;Maximum spindle speed, RPM
$31=0 ;Minimum spindle speed, RPM
$32=1 ;Laser-mode enable, boolean
$100=160.000 ;X-axis steps per millimeter
$101=160.000 ;Y-axis steps per millimeter
$102=160.000 ;Z-axis steps per millimeter
$110=3000.000 ;X-axis maximum rate, mm/min
$111=3000.000 ;Y-axis maximum rate, mm/min
$112=500.000 ;Z-axis maximum rate, mm/min
$120=100.000 ;X-axis acceleration, mm/sec^2
$121=100.000 ;Y-axis acceleration, mm/sec^2
$122=10.000 ;Z-axis acceleration, mm/sec^2
$130=435.000 ;X-axis maximum travel, millimeters
$131=305.000 ;Y-axis maximum travel, millimeters
$132=200.000 ;Z-axis maximum travel, millimeters

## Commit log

2023-02-01 arrancamos
    s
    [8x_M5x1mmSpacers.stl, 8x_M5x2mmSpacers.stl, 8x_M5x3mmSpacers.stl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]
2023-02-01 s
    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
    [Cantilevered_LaserEngraver_V821.3.xlsx, grbl_0819_2021.txt]
2023-02-02 acomodando archivos
    [LaserAirAssist_V4.stl, LaserAirAssist_V4_M.stl, Laser_focus_Wheel.stl]
2023-02-24 carro Z
    [6mmplate_with_beltclamp_v31.stl, base_slide_mount_long.stl, base_slide_mount_short.stl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]
2023-02-24 Z servo
    [UnoCNC_BackPanel.stl, UnoCNC_CaseBottom_w_2020_MountV2.stl, UnoCNC_CaseFront.stl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]
2023-02-24 Create case UNO cnc shield 2040 extrusion.step
    [case UNO cnc shield 2040 extrusion.step]
2023-02-27 Create Patas-imprimir 4.3mf
    [Patas-imprimir 4.3mf]
2023-03-27 Create base_slide_mount_short con soportes.3mf
    [base_slide_mount_short con soportes.3mf]
